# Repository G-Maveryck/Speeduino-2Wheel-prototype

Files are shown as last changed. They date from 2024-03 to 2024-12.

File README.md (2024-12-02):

# What is this ?
This project aim to build an Open-Source Engine Control Unit (aka ECU), fully programmable, accessible and modifiable, specificaly designed for motorcycles. It is still in "protoype" stage.
The goal is to end with a solution suited for retro-fit purposes : Lowering fuel consumption, pollution, and increased performances.

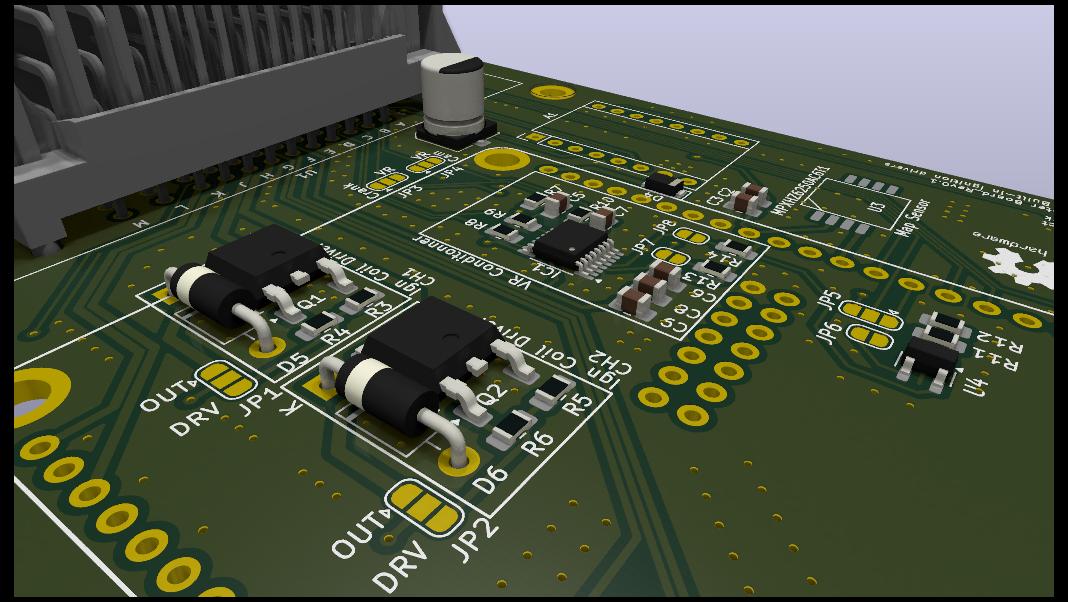
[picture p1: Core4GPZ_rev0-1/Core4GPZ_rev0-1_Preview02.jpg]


It's build around the DIY-EFI's CORE4 board, with a custom "Daughter board", and use the Speeduino firmware.
The CORE4 board is current choice for it's compact footprint, and fully featured board.
The Speeduino firmware can be found on it's own repo (See Licenses part for more informations.

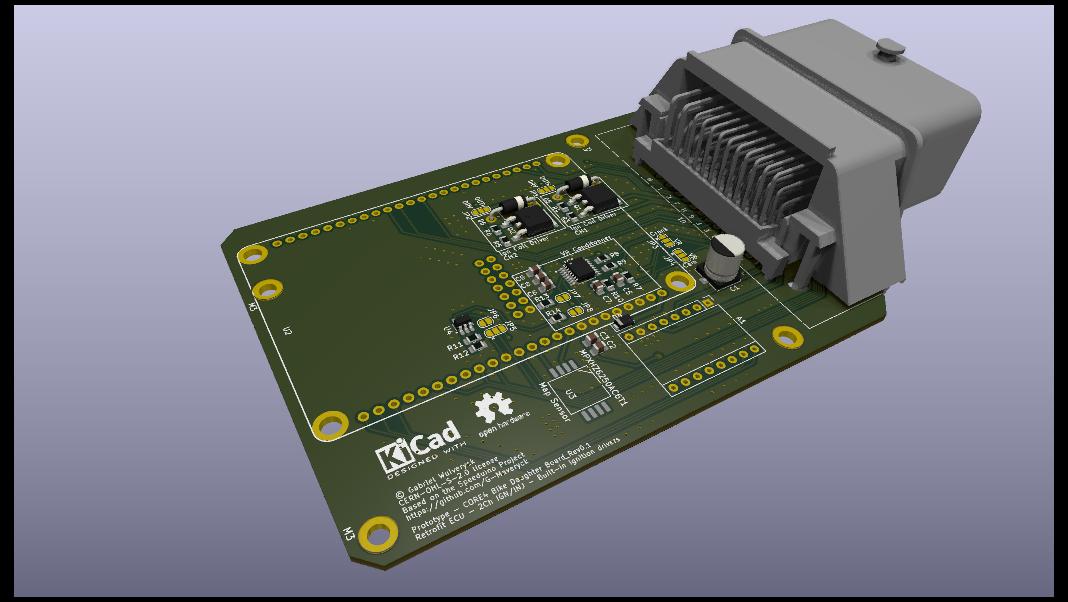
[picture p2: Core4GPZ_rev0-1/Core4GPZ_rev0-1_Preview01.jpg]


# Electronics and Hardware parts
As the CORE4 is kind of a "all-in-one" solution, this current project focuses on building a "Daughter board" to "host" the CORE4.
The CORE4 board implement the Arduino and the speeduino board, in the same board and a compact form factor.

The goal of the Daughter-Board is to implement all the electronics needed to work correctly, and to be mounted easily on a bike.
It include a proper automotive connector, routing the sensors signals to the pin of the CORE4, and implement the essential electronics directly on the board (see the "Specific parts" section for more informations).

In this early state (v0.1), the ignitions drivers, VR Conditionner and MAP Sensor are mounted directly on the board.

An aditional project can be found in the repository, aiming to build an external ignition driver. This is currently not finished, but is on the roadmap. 
Two different ignition drivers are planned : Classic IGBT transistor driver for coils, and a CDI Module (Capacitive Discharge Ignition).

# Workflow & Tools
The electronics parts (PCB and Schematics) are designed using KiCad EDA 8.0.
A specific Kicad symbols and footprint library is made for this project, and can be found on this repo (see : "KiCad_Library" directory)
If the library does not relink automatically, you can add it manually with "KiCad > Preferences > Configure symbols/Footprint library > Add existing library" )

The other CAD parts (eg. enclosure, boxes, etc..) are designed using Solidworks 2023, and additionnaly distributed in .STEP and .STL file format.

# Specific parts
For the purposes of this project, some parts have been selected as "default" part. This includes :
- Main I/O connector : Molex CMC 48way  - Black (500762-0481 PCB Header / 64320-3311 Female connector)
- MAP Sensor : MPXHZ6250-AC6T1 from Freescale
- Ignition Coil Driver : build around FGP3440G2-F085 IGBT transistor from On-Semi.
- VR Conditionners : Based on the "Dual VR Conditionner" from the official Speeduino project, with the MAX9926 chip. In this case, the circuit is directly welded on the board.

# Licenses
This project is distributed under the terms of the "CERN Open Hardware Licence Version 2 - Strongly Reciprocal" License.
See LICENSE.md for more information.

It is based on many open-source contributions, mainly the Speeduino Project (github :  https://github.com/noisymime/speeduino / https://github.com/speeduino/Hardware) wich is distributed under CERN Open Hardware License v2 Strong (CERN-OHL-S) for hardware, and GPL-2.0 for the firmware.
All informations about the DIY-EFI's CORE4 can be found here : https://diy-efi.co.uk/knowledge-base/core4-universal-getting-started

# Support and Contribution
If you want to get involved in this project, feel free to contribute, clone or fork this repo. Feel free to submit a pull request if you have any contribution.
To join the developpement, please contact me at : wulveryck.gabriel@gmail.com (more information on my Github profile)
A lot of work still need to be done. This include building, testing, and building the best and also cheaper solution for specific uses !
All help is welcome !

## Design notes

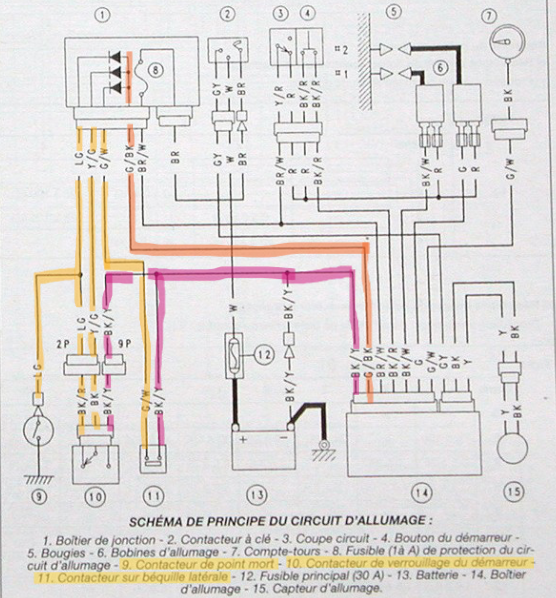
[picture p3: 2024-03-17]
Core4GPZ_rev0-1/ressources/Safety_Original_Diagram.png

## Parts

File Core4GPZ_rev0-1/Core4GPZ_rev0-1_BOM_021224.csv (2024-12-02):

Reference | Value | Datasheet | Footprint | Qty | DNP
A1 | Pololu_Breakout_DRV8825 | https://www.pololu.com/product/2982 | Module:Pololu_Breakout-16_15.2x20.3mm | 1
C1 | 100uF | ~ | Capacitor_SMD:CP_Elec_6.3x7.7 | 1
C2,C7 | 100nF | ~ | Capacitor_SMD:C_0805_2012Metric_Pad1.18x1.45mm_HandSolder | 2
C3,C8 | 1uF | ~ | Capacitor_SMD:C_0805_2012Metric_Pad1.18x1.45mm_HandSolder | 2
C4,C6 | 1nF | ~ | Capacitor_SMD:C_0805_2012Metric_Pad1.18x1.45mm_HandSolder | 2
C5 | 10nF | ~ | Capacitor_SMD:C_0805_2012Metric_Pad1.18x1.45mm_HandSolder | 1
D1,D2,D3 | 1N4448WX-TP | ~ | Diode_SMD:D_SOD-323_HandSoldering | 3
D4 | D_Schottky | ~ | Diode_SMD:D_PowerDI-123 | 1
D5,D6 | 1N4007 | ~ | Diode_THT:D_DO-41_SOD81_P10.16mm_Horizontal | 2
IC1 | MAX9926UAEE_V+ | https://componentsearchengine.com/Datasheets/1/MAX9926UAEE_V+.pdf | Package_SO:QSOP-16_3.9x4.9mm_P0.635mm | 1
Q1,Q2 | FGD3440G2-F085 | ~ | Package_TO_SOT_SMD:TO-252-2 | 2
R1,R2 | 100k | ~ | Resistor_SMD:R_0805_2012Metric_Pad1.20x1.40mm_HandSolder | 2
R3 | 660k | ~ | Resistor_SMD:R_0805_2012Metric_Pad1.20x1.40mm_HandSolder | 1
R4 | 300K | ~ | Resistor_SMD:R_0805_2012Metric_Pad1.20x1.40mm_HandSolder | 1
R5,R7,R9,R10,R11,R12 | 10k | ~ | -- valeurs mixtées -- | 6
R6,R8,R13,R14 | 1k | ~ | Resistor_SMD:R_0805_2012Metric_Pad1.20x1.40mm_HandSolder | 4
U1 | ~ | https://www.molex.com/en-us/products/part-detail/5007620481 | Bike_Prototype_LIB:Molex_CMC_48pin_Male_Black | 1
U2 | core4_rev1 | https://diy-efi.co.uk/knowledge-base/core4-universal-getting-started | Bike_Prototype_LIB:Core4 | 1
U3 | MPXHZ6250AC6T1 | https://www.nxp.com/docs/en/data-sheet/MPXH6250A.pdf | Bike_Prototype_LIB:MPXHZ6250AC6T1 | 1
U4 | LMV321 | http://www.ti.com/lit/ds/symlink/lmv324.pdf | Package_TO_SOT_SMD:SOT-23-5_HandSoldering | 1

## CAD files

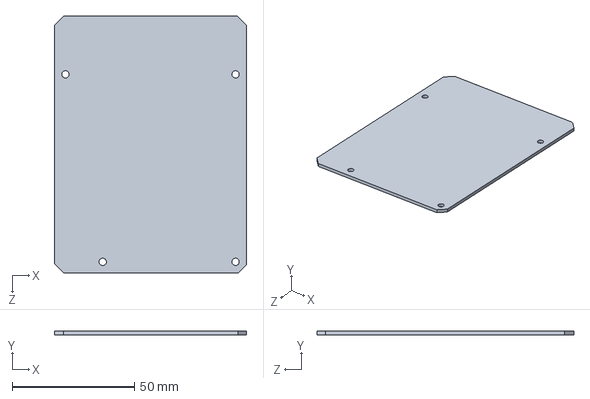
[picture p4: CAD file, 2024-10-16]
Enclosure_v0.1/CI.SLDPRT
78.7 x 1.60 x 105.2 mm

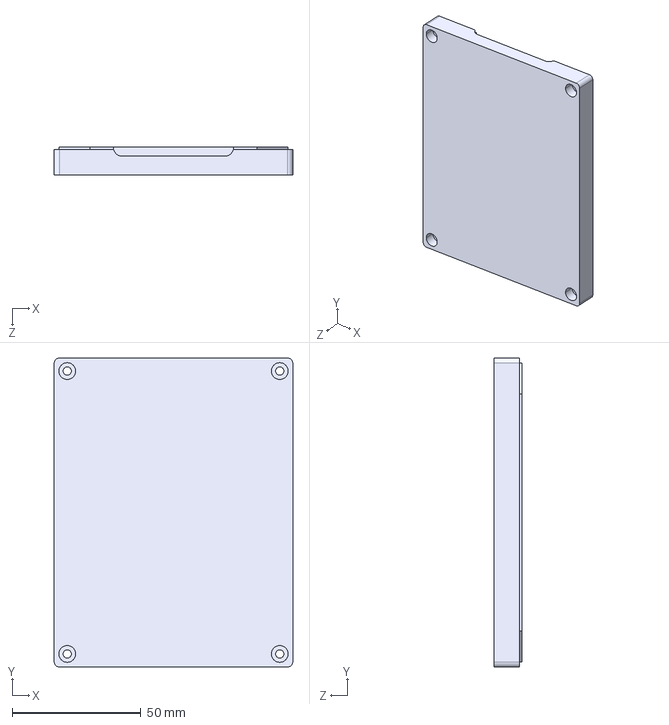
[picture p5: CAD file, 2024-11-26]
Enclosure_v0.1/STEP/Case_TOP.STEP
92.6 x 120.0 x 11.0 mm

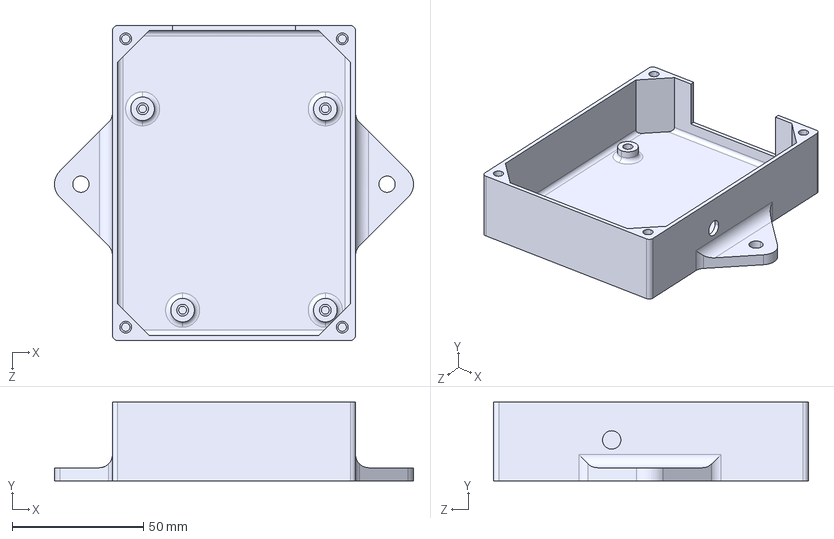
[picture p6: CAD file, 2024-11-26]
Enclosure_v0.1/STEP/Case_BOT.STEP
136.8 x 30.0 x 120.0 mm

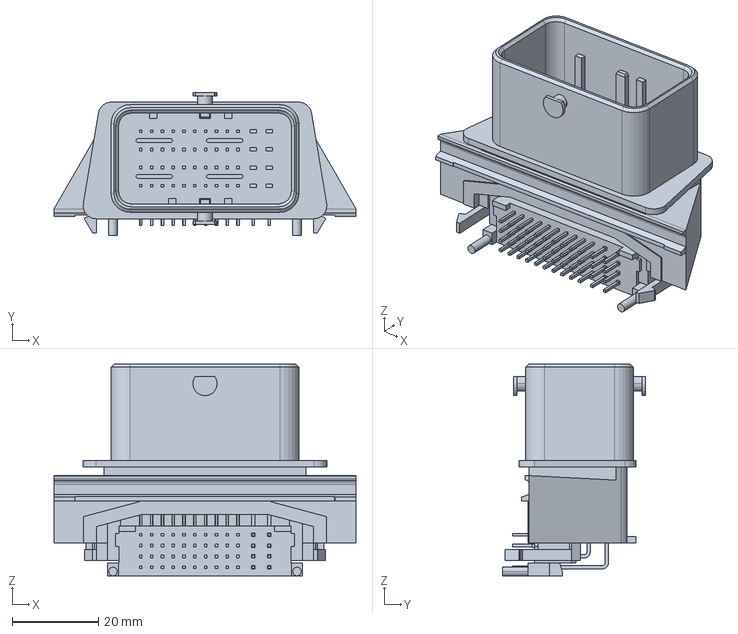
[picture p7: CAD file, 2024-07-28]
Enclosure_v0.1/5007620481.stp
69.9 x 33.2 x 49.0 mm

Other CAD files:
Enclosure_v0.1/Case_BOT.SLDPRT
Enclosure_v0.1/Case_TOP.SLDPRT
Enclosure_v0.1/STL/Case_BOT.STL
Enclosure_v0.1/STL/Case_TOP.STL

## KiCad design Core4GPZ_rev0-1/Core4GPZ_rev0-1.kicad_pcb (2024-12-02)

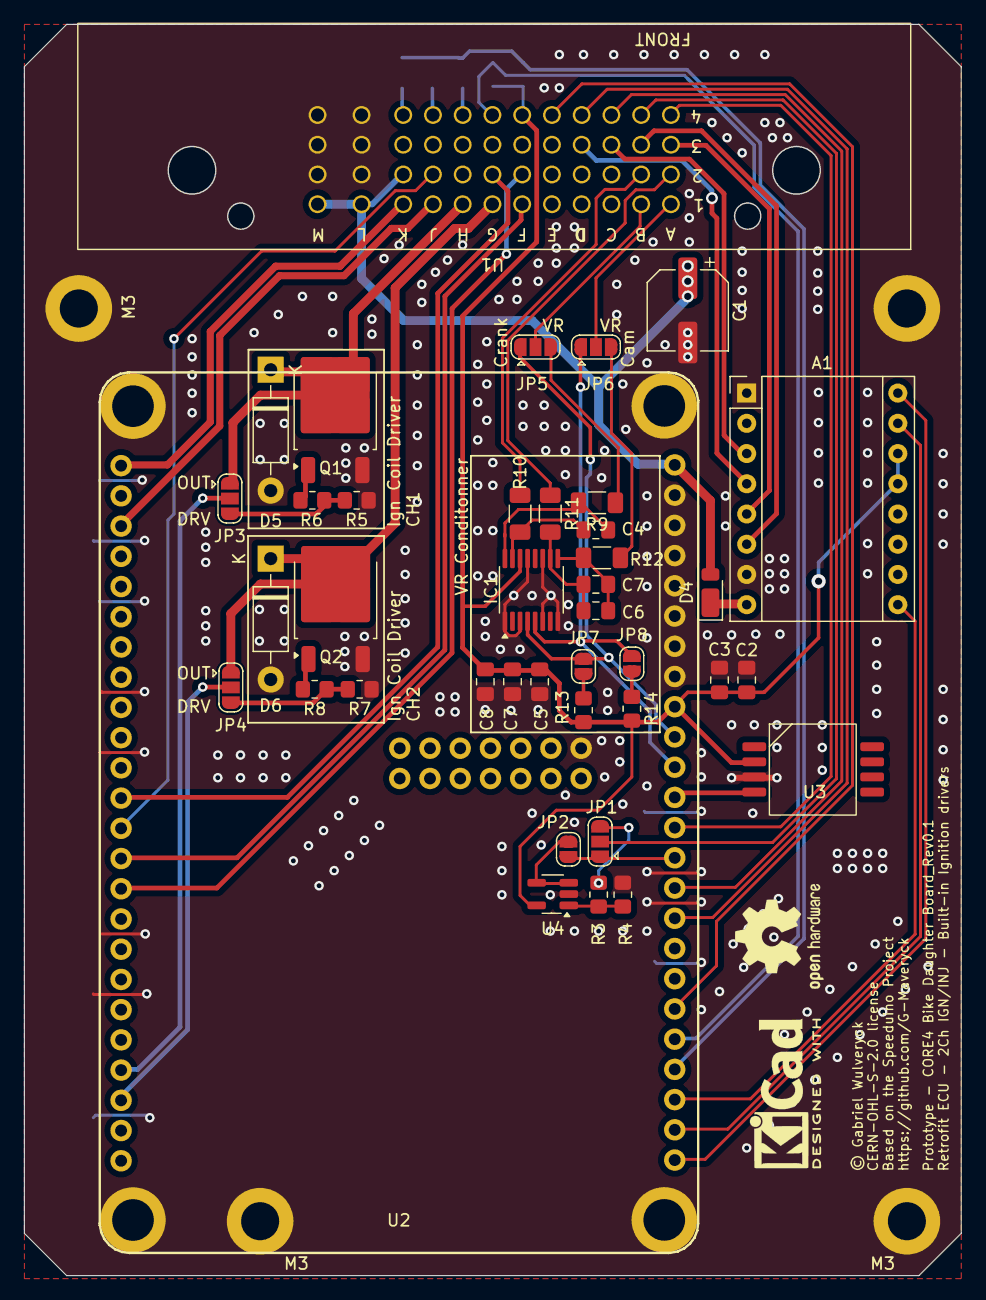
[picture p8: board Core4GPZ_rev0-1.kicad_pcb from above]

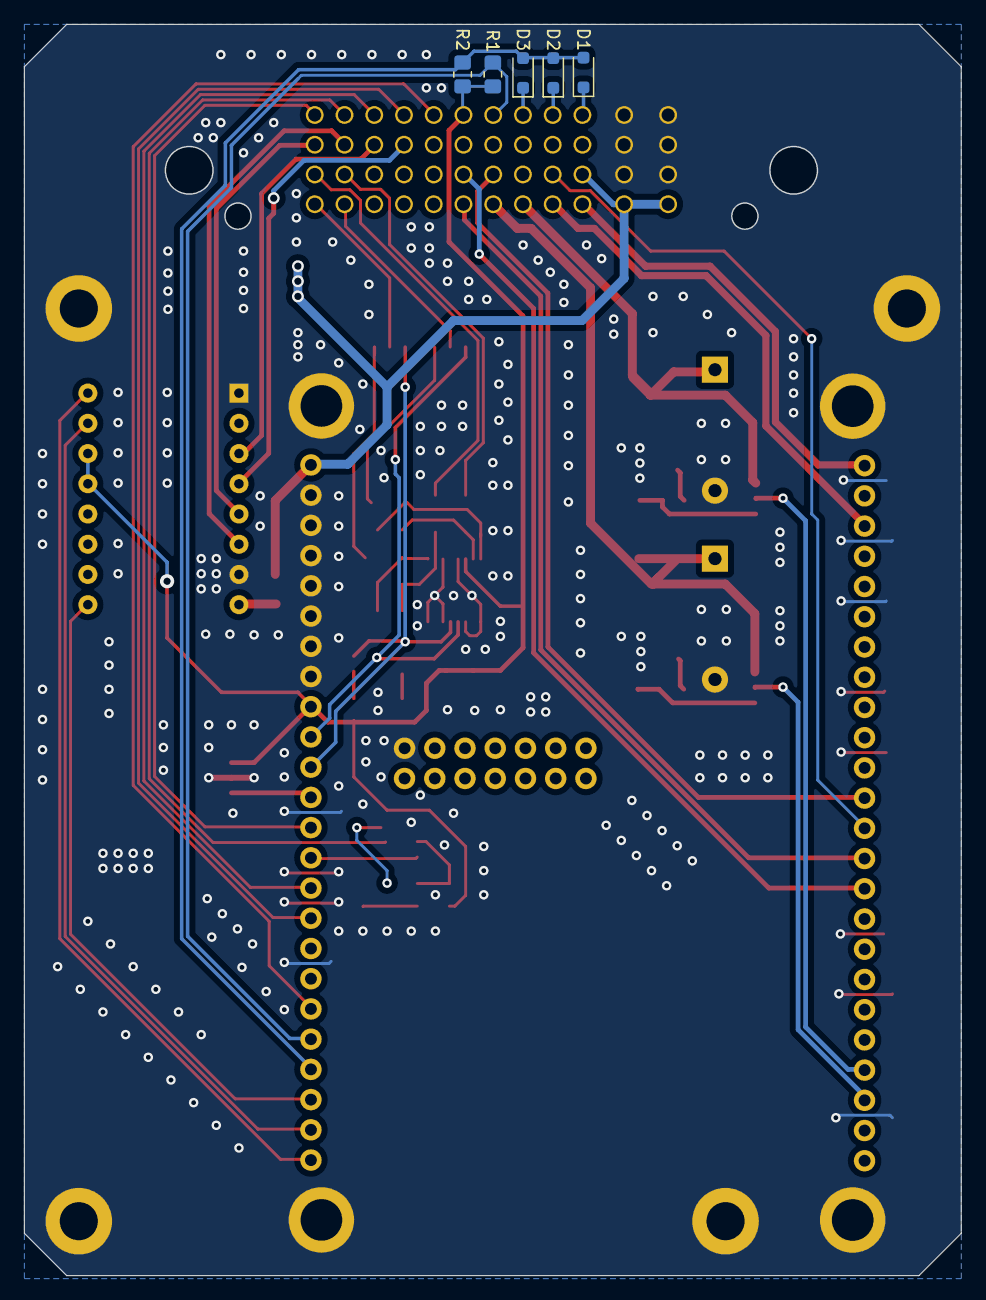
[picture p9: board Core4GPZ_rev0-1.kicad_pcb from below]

Board: 2 copper layers, 78.7 x 105.2 mm, 49 parts (5 on the bottom side), 54 nets.

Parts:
A1: Pololu_Breakout_DRV8825; Pololu_Breakout-16_15.2x20.3mm
C1: 100uF; CP_Elec_6.3x7.7
C2, C7: 100nF; C_0805_2012Metric_Pad1.18x1.45mm_HandSolder
C3, C8: 1uF; C_0805_2012Metric_Pad1.18x1.45mm_HandSolder
C4, C6, C7#2: 1nF; C_0805_2012Metric_Pad1.18x1.45mm_HandSolder
C5: 10nF; C_0805_2012Metric_Pad1.18x1.45mm_HandSolder
D1, D2, D3: 1N4448WX-TP; D_SOD-323_HandSoldering
D4: D_Schottky; D_PowerDI-123
D5, D6: 1N4007; D_DO-41_SOD81_P10.16mm_Horizontal
IC1: MAX9926UAEE_V+; QSOP-16_3.9x4.9mm_P0.635mm
JP1, JP3, JP4: SolderJumper_3_Open; SolderJumper-3_P1.3mm_Open_RoundedPad1.0x1.5mm
JP2: SolderJumper_2_Open; SolderJumper-2_P1.3mm_Open_RoundedPad1.0x1.5mm
JP5: CRANK - VR/Hall Selector; SolderJumper-3_P1.3mm_Open_RoundedPad1.0x1.5mm
JP6: CAM - VR/Hall Selector; SolderJumper-3_P1.3mm_Open_RoundedPad1.0x1.5mm
JP7: Crank Pull-Up; SolderJumper-2_P1.3mm_Open_RoundedPad1.0x1.5mm
JP8: Cam Pull-up; SolderJumper-2_P1.3mm_Open_RoundedPad1.0x1.5mm
M3, M3#2, M3#3, M3#4: MountingHole_3.2mm_M3_DIN965_Pad
Q1, Q2: FGD3440G2-F085; TO-252-2
R1, R2: 100k; R_0805_2012Metric_Pad1.20x1.40mm_HandSolder
R3: 660k; R_0805_2012Metric_Pad1.20x1.40mm_HandSolder
R4: 300K; R_0805_2012Metric_Pad1.20x1.40mm_HandSolder
R5, R7: 10k; R_0805_2012Metric_Pad1.20x1.40mm_HandSolder
R6, R8, R13, R14: 1k; R_0805_2012Metric_Pad1.20x1.40mm_HandSolder
R9, R10, R11, R12: 10k; R_1206_3216Metric_Pad1.30x1.75mm_HandSolder
U1: Molex_CMC_48pin_Male_Black
U2: core4_rev1; Core4
U3: MPXHZ6250AC6T1
U4: LMV321; SOT-23-5_HandSoldering

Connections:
/02_SNSR: U1.34 (4D), U2.40 (02)
/FAN_CTL: U1.16 (2F), U2.15 (FAN)
/FLEX_SNSR: U1.35 (4E), U2.43 (FLEX)
/FUEL_PUMP: U1.6 (1F), U2.14 (FUELP)
/IAT_SNSR: U1.33 (4C), U2.39 (IAT)
/IDLE_1: U1.17 (2G), U2.12 (IDLED1)
/INJ1_TRIG: U1.10 (1K), U2.1 (INJ1)
/INJ2_TRIG: U1.9 (1J), U2.3 (INJ2)
/TACHO_OUT: U1.19 (2J), U2.13 (TACHO)
/TPS_SNSR: U1.31 (4A), U2.37 (TPS)
BIKE_+12V_SWITCHED_IN: C1.1, D4.2 (A), U1.20 (2K), U1.41 (1L), U1.42 (1M), U2.25 (+12V)
CAM_SIGNAL: IC1.5 (COUT2), JP6.1 (A), JP8.1 (A), U2.35 (RPM2)
CAM_SNSR: JP6.2 (C), U1.1 (1A)
CAM_SNSR_VR-: R11.1, U1.11 (2A)
CLT_5V: JP1.1 (A), JP2.1 (A), U2.38 (CLT)
CLT_SNSR: JP1.2 (C), U1.32 (4B)
CRANK_SIGNAL: IC1.4 (COUT1), JP5.1 (A), JP7.1 (A), U2.34 (RPM1)
CRANK_SNSR: JP5.2 (C), U1.2 (1B)
CRANK_SNSR_VR-: R10.1, U1.12 (2B)
Clutch_SW: D2.1 (K), U1.39 (4J)
DIR: A1.16 (DIR), U2.48 (DIR)
EN: A1.9 (~EN), U2.46 (ENBL)
GND: A1.1 (GND), A1.7 (GND), C1.2, C2.2, C3.2, C5.2, C7.2, C8.2, D5.2 (A), D6.2 (A), IC1.1 (IN_THRS1), IC1.3 (BIAS1), IC1.6 (BIAS2), IC1.8 (INT_THRS2), IC1.11 (GND), IC1.13 (ZERO_EN), M3.1, M3#2.1, M3#3.1, M3#4.1, Q1.3 (E), Q2.3 (E), R4.2, R5.1, R7.1, U1.43 (2L), U1.44 (2M), U1.45 (3L), U1.46 (3M), U1.47 (4L), U1.48 (4M), U2.26 (EARTH), U2.27 (EARTH), U2.28 (EARTH), U2.29 (EARTH), U2.30 (EARTH), U2.31 (EARTH), U2.32 (EARTH), U2.61 (EARTH), U2.101, U2.102, U2.103, U2.104, U3.3 (GND), U4.2 (V-)
IGN_COIL1_DRIVE: D5.1 (K), JP3.1 (A), Q1.2 (C), U1.8 (1H)
IGN_COIL2_DRIVE: D6.1 (K), JP4.1 (A), Q2.2 (C), U1.7 (1G)
IGN_TRIG_1: JP3.2 (C), U2.21 (IGN1)
IGN_TRIG_2: JP4.2 (C), U2.22 (IGN2)
NEUTRAL_SW: D3.1 (K), U1.38 (4H)
unnamed: A1.8 (VMOT), D4.1 (K)
unnamed: C4.1, IC1.16 (IN1+), R9.2
unnamed: C4.2, IC1.15 (IN1-), R10.2
unnamed: C6.2, C7#2.2, IC1.9 (IN2+), R12.2
unnamed: C6.1, C7#2.1, IC1.10 (IN2-), R11.2
unnamed: JP1.3 (B), R3.1
unnamed: JP2.2 (B), U4.3 (-), U4.4
unnamed: JP3.3 (B), R5.2, R6.2
unnamed: JP4.3 (B), R7.2, R8.2
unnamed: JP5.3 (B), R9.1
unnamed: JP6.3 (B), R12.1
unnamed: JP7.2 (B), R13.1
unnamed: JP8.2 (B), R14.1
unnamed: Q1.1 (G), R6.1
unnamed: Q2.1 (G), R8.1
unnamed: U2.36 (MAP_IN), U3.4 (Vout)
unnamed: R3.2, R4.1, U4.1 (+)
SAFE_SIGNAL: D1.2 (A), D2.2 (A), D3.2 (A), R2.2, U2.45 (SPR_IN2)
SHIFT+: R1.2, U1.37 (4G), U2.44 (SPR_IN1)
SNSR_+5V: A1.13 (~RST), A1.14 (~SLP), C2.1, C3.1, C5.1, C7.1, C8.1, IC1.14 (VCC), R1.1, R2.1, R13.2, R14.2, U1.36 (4F), U2.33 (+5V), U3.2 (Vs), U4.5 (V+)
STEP: A1.15 (STEP), U2.47 (STEP)
SideStand_SW: D1.1 (K), U1.40 (4K)
Stepper_A1: A1.4 (A1), U1.24 (3D)
Stepper_A2: A1.3 (A2), U1.23 (3C)
Stepper_B1: A1.5 (B1), U1.21 (3A)
Stepper_B2: A1.6 (B2), U1.22 (3B)

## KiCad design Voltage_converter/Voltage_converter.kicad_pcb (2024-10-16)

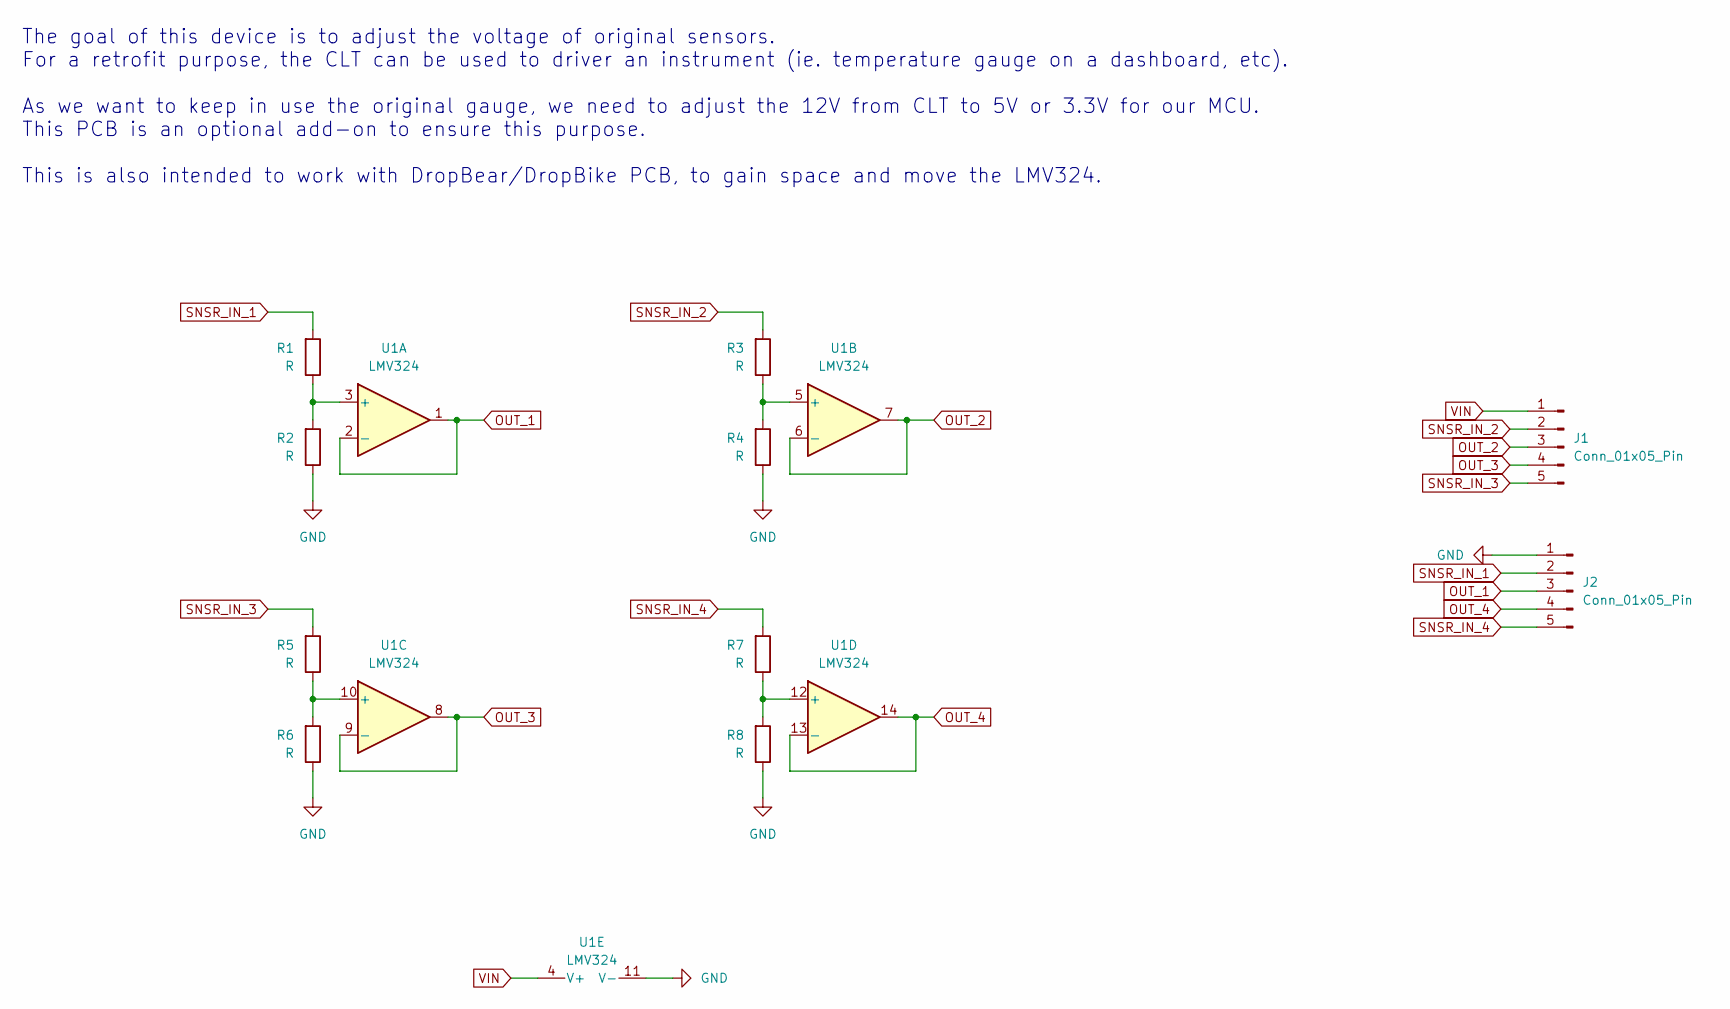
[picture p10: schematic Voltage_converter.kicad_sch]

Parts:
J1, J2: Conn_01x05_Pin; PinHeader_1x05_P2.54mm_Vertical
R1, R2, R3, R4, R5, R6, R7, R8: R; R_0805_2012Metric_Pad1.20x1.40mm_HandSolder
U1: LMV324; SOIC-14_3.9x8.7mm_P1.27mm

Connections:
GND: J2.1, R2.1, R4.1, R6.1, R8.1, U1.11 (V-)
unnamed: R1.1, R2.2, U1.3 (+)
unnamed: R3.1, R4.2, U1.5 (+)
unnamed: R5.1, R6.2, U1.10 (+)
unnamed: R7.1, R8.2, U1.12 (+)
OUT_1: J2.3, U1.1, U1.2 (-)
OUT_2: J1.3, U1.6 (-), U1.7
OUT_3: J1.4, U1.8, U1.9 (-)
OUT_4: J2.4, U1.13 (-), U1.14
SNSR_IN_1: J2.2, R1.2
SNSR_IN_2: J1.2, R3.2
SNSR_IN_3: J1.5, R5.2
SNSR_IN_4: J2.5, R7.2
VIN: J1.1, U1.4 (V+)

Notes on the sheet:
The goal of this device is to adjust the voltage of original sensors. For a retrofit purpose, the CLT can be used to driver an instrument (ie. temperature gauge on a dashboard, etc). As we want to keep in use the original gauge, we need to adjust the 12V from CLT to 5V or 3.3V for our MCU. This PCB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

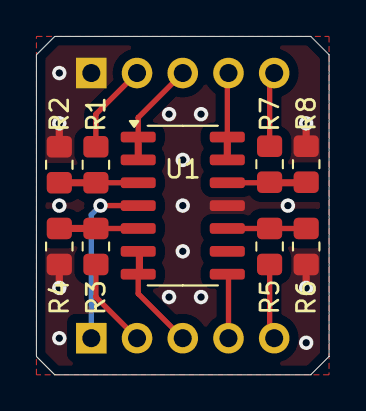
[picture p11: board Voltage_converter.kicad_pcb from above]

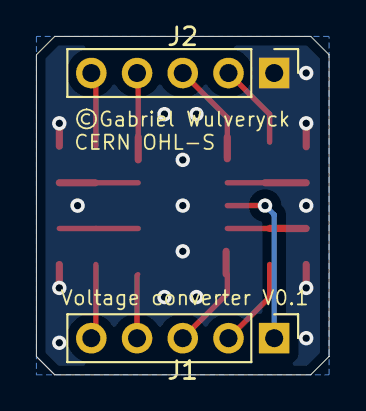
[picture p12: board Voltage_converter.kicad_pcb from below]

Board: 2 copper layers, 16.3 x 18.8 mm, 11 parts (2 on the bottom side), 14 nets.

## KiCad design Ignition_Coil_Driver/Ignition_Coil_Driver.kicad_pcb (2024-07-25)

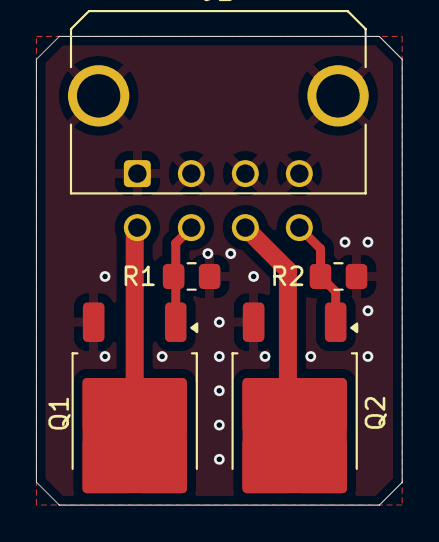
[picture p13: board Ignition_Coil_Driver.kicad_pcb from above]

Board: 2 copper layers, 20.3 x 26.0 mm, 5 parts (0 on the bottom side), 5 nets.

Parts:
J1: Conn_02x04_Row_Letter_First; Molex_Micro-Fit_3.0_43045-0821_2x04-1MP_P3.00mm_Horizontal
Q1, Q2: FGD3440G2-F085; TO-252-2
R1, R2: 1k; R_0805_2012Metric_Pad1.20x1.40mm_HandSolder

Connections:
COIL1_Drive: J1.5, Q1.2 (C)
COIL2_Drive: J1.7, Q2.2 (C)
GND: J1.1, J1.2, J1.3, J1.4, J1.MP, Q1.3 (E), Q2.3 (E), R1.2, R2.2
IGN_TRIG_1: J1.6, Q1.1 (G), R1.1
IGN_TRIG_2: J1.8, Q2.1 (G), R2.1

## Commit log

2024-02-24 Add a splited CDI module. First Design of Ignition coil driver
    [CDI_Module.kicad_pcb, CDI_Module.kicad_sch, Core4GPZ.kicad_sch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]
2024-03-17 Updated security wiring and changed IGN driver for MOSFET
    [CDI_Module.kicad_sch, Core4GPZ.kicad_pcb, Core4GPZ.kicad_sch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]
2024-03-23 First Drawing of High volatage generator part
    First Drawing of High volatage generator part
    [CDI_Module.kicad_sch, HV_gen.kicad_sch]
2024-03-26 Changed Connectors for Molex CMC 48pins Black.
    Changed ECU Connector for Molex CMC 48pins Black, for compacity and cost reduction. Designed custom Footprint for this purpose
    [CDI_Module.kicad_sch, Core4GPZ.kicad_pcb, Core4GPZ.kicad_sch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]
2024-03-27 Test montage générateur de Haute tension
    [Core4GPZ.kicad_pcb, Core4GPZ.kicad_sch, HV_gen.kicad_sch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]
2024-03-31 Redraw CDI pwr Supply with Boost circuit for 48v output
    [CDI_Module.kicad_pcb, CDI_Module.kicad_sch, HV_gen.kicad_sch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]
2024-04-04 Updated to Kicad 8.0
    Also added Highvoltage circuit
    [CDI_Module.kicad_sch, Core4GPZ.kicad_sch, HV_pwr_sply.kicad_sch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]
2024-04-05 Added documentation for Molex Connector
2024-04-27 Work in progress
    [CDI_Module.kicad_sch, HV_pwr_sply.kicad_sch]
2024-05-03 Added VR Conditionner for Cam/Crank SNSR
    Added some jumper for prototyping and testing purposes
    [Core4GPZ.kicad_pcb, Core4GPZ.kicad_sch, Ignition_Driver.kicad_sch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]
2024-05-08 Started Implementation of VR Conditionner
    [Core4GPZ.kicad_pcb, Core4GPZ.kicad_sch, Ignition_Driver.kicad_sch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]
2024-05-16 Implemented VR_Conditionner (MAX9926+)
    First look at ground plane
    [Core4GPZ.kicad_pcb, Core4GPZ.kicad_sch, Core4GPZ_Hor.kicad_pcb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]
2024-06-18 Added rev0.1 dir
    Aim to re draw a cleaner PCB, with cleaner routes
    [Core4GPZ_rev0-1.kicad_pcb, Core4GPZ_rev0-1.kicad_sch, Ignition_Driver.kicad_sch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]
2024-06-18 Frist revision
    First revision finished, optimised routing, board turned 180°.
    [Core4GPZ_rev0-1.kicad_pcb, Core4GPZ_rev0-1.kicad_sch]
2024-06-18 Tiny modification
    ???
    [CDI_Module.kicad_sch, Core4GPZ.kicad_pcb, Core4GPZ.kicad_sch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]
2024-06-19 Finalized ground planes
    Added CORE4 pads to ground
    [Core4GPZ_rev0-1.kicad_pcb]
2024-07-25 Rewied ground plane, set all SNSR+5V ref to one pin
    [Core4GPZ_rev0-1.kicad_pcb, Core4GPZ_rev0-1.kicad_sch, pwr_supply.kicad_sch]
2024-07-25 Designed a minimal external coil driver
    [HV_pwr_sply.kicad_sch, Ignition_Coil_Driver.kicad_pcb, Ignition_Coil_Driver.kicad_sch]
2024-07-25 Added informations for Molex CMC conn
    [Core4GPZ_rev0-1.kicad_sch]
2024-07-27 Deleted first version (outdated)
    [Core4GPZ.kicad_pcb, Core4GPZ.kicad_sch, Core4GPZ_Hor.kicad_pcb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]
2024-07-27 Added first enclosure design
    [ASS_CASE.SLDASM, CI.SLDPRT, Case_BOT.SLDPRT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]
2024-07-28 Added CAD enclosure .step and .stl
    [5007620481.stp, ASS_CASE.SLDASM, CI.SLDPRT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]
2024-08-13 Reworked the VR conditionner
    Schematic and PCB based on the Dropbear model
    [Core4GPZ_rev0-1.kicad_pcb, Core4GPZ_rev0-1.kicad_sch, Ignition_Driver.kicad_sch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]
2024-08-14 Moved VR Conditionner.
    [Core4GPZ_rev0-1.kicad_pcb, Core4GPZ_rev0-1.kicad_sch]
2024-08-15 Moved +12V decoupling capacitors
    [Core4GPZ_rev0-1.kicad_pcb, VR_Conditionner.kicad_sch, pwr_supply.kicad_sch]
2024-08-18 Changed MAP sensors for MPXHZ6250AC6T1
    [Core4GPZ_rev0-1.kicad_pcb, Core4GPZ_rev0-1.kicad_sch, pwr_supply.kicad_sch]
2024-08-29 Modified GND Plane. Reworked routing
    [Core4GPZ_rev0-1.kicad_pcb, Core4GPZ_rev0-1.kicad_sch, Ignition_Driver.kicad_sch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]
2024-09-10 Started implementing Stepper driver
    DRV8825 breakout board
    [Core4GPZ_rev0-1.kicad_sch]
2024-09-12 Implemented DRV8825 and upgrade IGN Driver
    Ignition drivers upgraded with SMD IGBT FGD3440
    Added Stepper Driver DRV8825
    [Core4GPZ_rev0-1.kicad_pcb, Core4GPZ_rev0-1.kicad_sch, Ignition_Driver.kicad_sch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]
2024-09-13 Reduced board width
    moved IGN Driver under the Core4 to reduce overall board size
    [Core4GPZ_rev0-1.kicad_pcb, Core4GPZ_rev0-1.kicad_sch]
2024-09-26 Minor visual modifications
    [Core4GPZ_rev0-1.kicad_pcb]
2024-10-16 Added AOP for a proper decoupling for CLT
    Modified Fixing point and dimensions on the enclosure
    [CI.SLDPRT, Case_BOT.SLDPRT, Case_TOP.SLDPRT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]
2024-10-17 Removed NeutralSwitch. Added Up-Shifter support
    [Core4GPZ_rev0-1.kicad_pcb, Core4GPZ_rev0-1.kicad_sch, Safety.kicad_sch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]
2024-10-22 Reorganised Schematic
    [Core4GPZ_rev0-1.kicad_pcb, Core4GPZ_rev0-1.kicad_sch, Ignition_Driver.kicad_sch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]
2024-10-23 Added pullup resistor on VR Conditionner
    [Core4GPZ_rev0-1.kicad_pcb, Core4GPZ_rev0-1.kicad_sch, VR_Conditionner.kicad_sch]
2024-11-12 Added Gerber files
    [Core4GPZ_rev0-1-B_Cu.gbr, Core4GPZ_rev0-1-B_Mask.gbr, Core4GPZ_rev0-1-B_Paste.gbr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]
2024-11-26 Updated CAD Enclosure STL and STEP export
    [5007620481.stp, CI.SLDPRT, Case_BOT.SLDPRT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]
2024-11-27 Updated component Library with specific parts
    Added "Speeduino_bike_prototype" library, with symbols and footprints.
    You can add this library to your library table.
    [Core4GPZ_rev0-1-B_Cu.gbr, Core4GPZ_rev0-1-B_Mask.gbr, Core4GPZ_rev0-1-B_Paste.gbr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]
2024-11-27 Updated gerber, updated BOM
    Also added preview files in JPG
    [Core4GPZ_rev0-1_BOM_131124.csv, Core4GPZ_rev0-1_BOM_151124.csv, inputs.kicad_sch]
2024-12-02 Updated project library, BOM and documentation
    [Core4GPZ_rev0-1-B_Cu.gbr, Core4GPZ_rev0-1-B_Mask.gbr, Core4GPZ_rev0-1-B_Paste.gbr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]

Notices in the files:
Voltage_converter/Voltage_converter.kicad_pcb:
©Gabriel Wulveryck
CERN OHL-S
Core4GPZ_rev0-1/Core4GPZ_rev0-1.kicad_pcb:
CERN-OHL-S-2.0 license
